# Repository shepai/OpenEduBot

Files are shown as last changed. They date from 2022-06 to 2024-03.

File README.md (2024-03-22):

# OpenEduBot
Python library and robotics building instructions for robotics education within schools. The aim of this project is to provide ease of teaching and programming with MicroPython, and reduce the cost of teaching robotics. Teaching physical robotics is engaging and rewarding. Students gain experience in coding, engineering and electronics, compared to making cheap existing kits that do not combine any of these.

## Robot library
We have written a robotics library that allow connection with each chassis. The library must be placed in the same directory as the code running on the Pico. This can be done using [Thonny IDE](https://thonny.org/)

Once the library is installed on the device.

There are two variants of the library, a circuitPython and a microPython. The circuitPython can work with both the Pico and PiMaker rp2040. The microPython one is designed for the Raspberry Pi Pico. 

## Building a chassis
This Github contains the instructions and demo code for each chassis. Parts lists can be found under each robot, as well as links to places the parts can be purchased. The item names are there, so it is up to you where you purchase thee parts from.

## The different bots
The robots all make use of the Raspberry Pi Pico, which allows programming through Python! Python is a simple language to learn for those starting to learn code.

### WheelBot
Wheelbot uses two DC motors and a ball caster at the front. This robot uses a simple design, but can exhibit some intelligent behaviour. Whether you want to use ultrasound sensors to make robot vacum-cleaner algorithms, or light following bots - your imagination (and the use of wheels) is your limit.

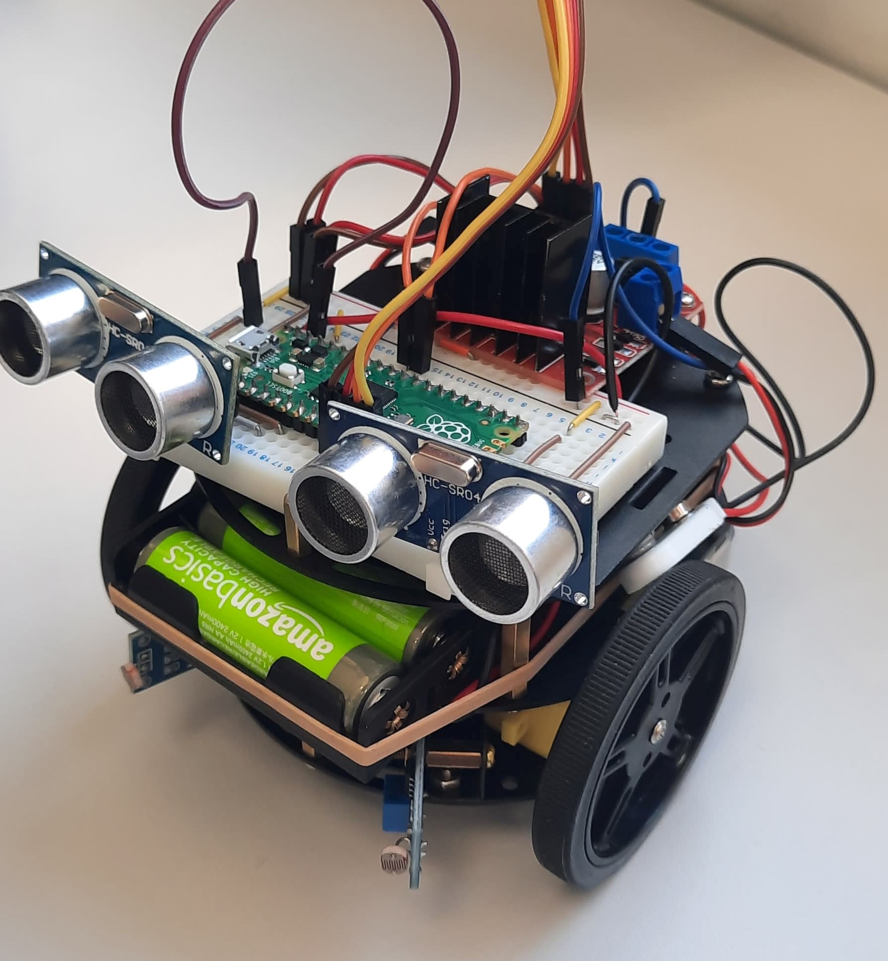
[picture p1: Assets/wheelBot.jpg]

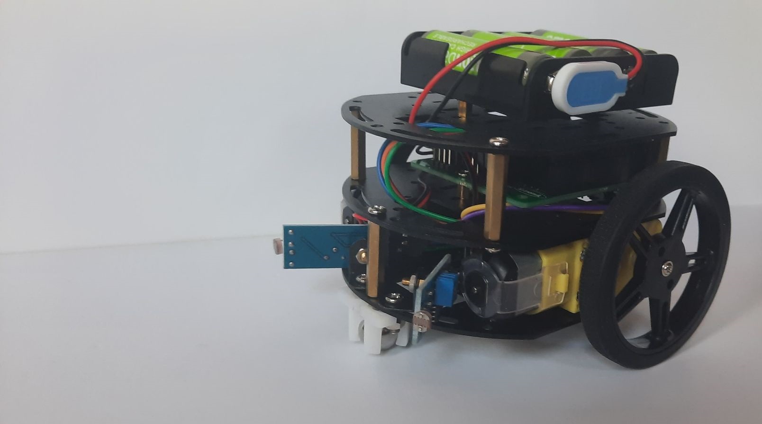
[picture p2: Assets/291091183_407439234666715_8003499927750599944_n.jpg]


## Credits
This project was worked on by University of Sussex students:

Dexter R Shepherd*, https://www.linkedin.com/in/dexter-shepherd-1a4a991b8/

Joshua Kybett, https://www.linkedin.com/in/jkybett/

Eliseo Dalle Crode,https://www.linkedin.com/in/eliseo-dalle-crode-613557104/

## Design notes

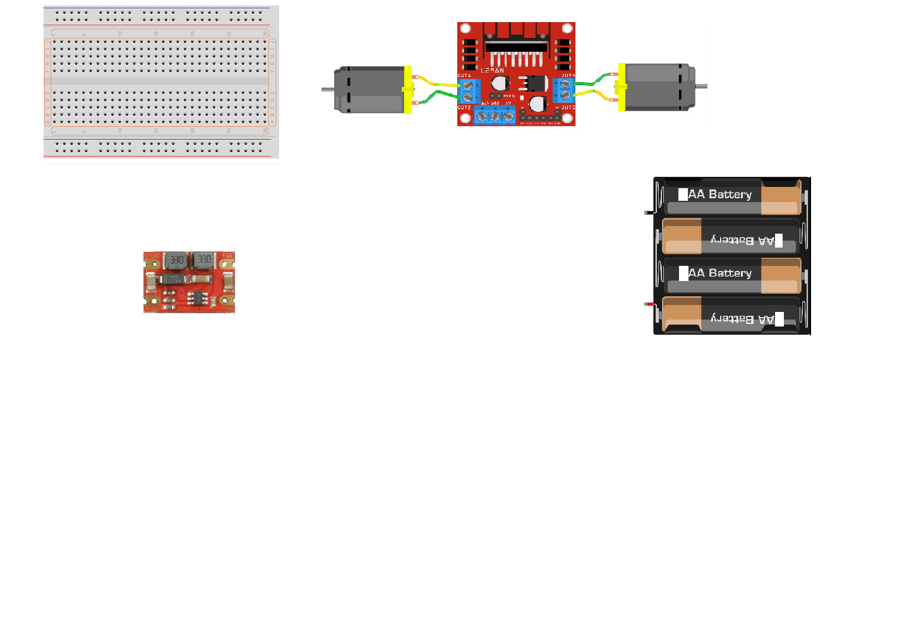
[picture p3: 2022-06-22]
Assets/electronics.png

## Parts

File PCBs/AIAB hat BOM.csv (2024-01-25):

Designator | Footprint | Quantity | Comments | Supplier and ref
HP4067 | SSOP-24_5.3x8.2mm_P0.65mm | 1 | SSOP-24_5.3x8.2mm_P0.65mm
R12,R5,R6,R7 | R_0603_1608Metric | 4 | 1k
APM | PinHeader_1x05_P2.54mm_Vertical | 1 | PinHeader_1x05_P2.54mm_Vertical
C6 | C_0603_1608Metric | 1 | 10uF
D1,D2 | R_LDR_5.1x4.3mm_P3.4mm_Vertical | 2 | R_LDR_5.1x4.3mm_P3.4mm_Vertical
C5 | C_0603_1608Metric | 1 | 4.7uF
Ultra sound,F2,F1 | PinHeader_1x04_P2.54mm_Vertical | 3 | PinHeader_1x04_P2.54mm_Vertical
X1 | MICROSD | 1 | MICROSD
C4 | C_0603_1608Metric | 1 | 220pF
Powerswitch | SW_DIP_SPSTx01_Slide_6.7x4.1mm_W6.73mm_P2.54mm_LowProfile_JPin | 1 | SW_DIP_SPSTx01_Slide_6.7x4.1mm_W6.73mm_P2.54mm_LowProfile_JPin
M12,M11,Power | TerminalBlock_Altech_AK300-2_P5.00mm | 3 | TerminalBlock_Altech_AK300-2_P5.00mm
I2C,POWER2,AP | PinHeader_1x02_P2.54mm_Vertical | 3 | PinHeader_1x02_P2.54mm_Vertical
C4M | 0805-NO | 1 | 10uF
PI | RPi_Pico_SMD_TH | 1 | RPi_Pico_SMD_TH
MDrive | DIP-16_W10.16mm | 1 | DIP-16_W10.16mm
R2,R1,R3,R4 | R_0603_1608Metric | 4 | 4.7k
R8 | R0805 | 1 | 1K
VR | SOT-223-3_TabPin2 | 1 | SOT-223-3_TabPin2
C7,C2,C1,C3 | C_0603_1608Metric | 4 | 0.1uF
R11,R10 | RESPACK_4X0603 | 2 | 10K
C2B | E3,5-8 | 1
U1 | TSSOP28 | 1 | PCA9685
IC1 | SO16 | 1 | 4050D
D3 | LED_0603_1608Metric | 1 | LED_Small_Filled
U2 | SOT-23-5 | 1 | AP2112K-3.3
U4 | InvenSense_QFN-24_4x4mm_P0.5mm | 1 | MPU-6050
ACT0 | CHIP-LED0805 | 1 | RED
JP2 | 3X04 | 1
R9 | RESPACK_4X0603 | 1 | 220

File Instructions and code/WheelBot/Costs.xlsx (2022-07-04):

 |  |  |  | No. of robots
 |  |  |  | 1
One robot
Part | Quantity | Price | Subtotal | Link |  |  |  |  |  | Key
Chassis | 1 | 23.7 | 23.7 | https://thepihut.com/products/adafruit-mini-3-layer-round-robot-chassis-kit-2wd-with-dc-motors |  |  |  |  |  | PiHut
Robotics HAT | 1 | 13.75 | 13.75 | https://uk.rs-online.com/web/p/raspberry-pi-hats-add-ons/2247771 |  |  |  |  |  | RS
Battery holder | 1 | 0.808 | 0.808 |  |  |  |  |  |  | Amazon
Batteries | 4 | 0.608 | 2.432 |  |  |  |  |  |  | Farnell
Screwdriver set | 1 | 0.8106666667 | 0.8106666667
Pico | 1 | 3.276 | 3.276
USB cable | 1 |  | 0
Battey wire | 1 | 0.317 | 0.317 |  |  |  | Overall total | Tax estimate | Total estimate
Sensors | 4 | 0.5592 | 2.2368 |  |  |  | £1700.30 | £340.06 | £2040.36
Bracket | 4 | 0.0932 | 0.3728
Jumper wires | 12 | 0.03745 | 0.4494
M3 screws | 12 | 0.21 | 2.52
GPIO pins | 40 | 0.003596 | 0.14384
Standoffs | 6 | 0.176 | 1.056
Total | 89 | £44.35 | £51.87
Mass parts | Price | Per unit | Pack No. | Min Quantity | Subtotal | Link
480 Picos | 1572.48 | 3.276 | 480 | 1 | 1572.48 | https://uk.rs-online.com/web/p/raspberry-pi/2122161
Jumper wire pack | 7.49 | 0.03745 | 200 | 1 | 7.49 | https://www.amazon.co.uk/AZDelivery-Jumper-Arduino-Raspberry-Breadboard/dp/B07KFMSW7H
Battery wire 100 | 31.7 | 0.317 | 100 | 1 | 31.7 | https://uk.rs-online.com/web/p/battery-contacts/0489021A
Brackets | 5.592 | 0.0932 | 60 | 1 | 5.592 | https://www.amazon.co.uk/gp/product/B07RBJN9YF/ref=ppx_yo_dt_b_search_asin_title?ie=UTF8&psc=1
Battery pack (25) | 20.2 | 0.808 | 25 | 1 | 20.2 | https://uk.farnell.com/multicomp-pro/mp000316/battery-holder-aa-snap-on/dp/3126550
GPIO pins | 7.192 | 0.003596 | 2000 | 1 | 7.192 | https://www.amazon.co.uk/Pack-Single-2-54-Header-Connector/dp/B06XR8CV8P
MH sensor 10 | 5.592 | 0.5592 | 10 | 1 | 5.592 | https://www.amazon.co.uk/DollaTek-Digital-Intensity-Resistor-Photoresistor/dp/B07DJ4CMF7
GPIO pins bent | 8.4 | 0.84 | 10 | 1 | 8.4 | https://uk.farnell.com/samtec/tsm-106-01-l-sv/header-2-54mm-smt-1x6way/dp/1885916?mckv=_dc|pcrid|565467377247|plid||kword||match||slid||product|1885916|pgrid|125527087130|ptaid|pla-1641699961606|&CMP=KNC-GUK-GEN-SHOPPING-SMART-AUTOMATION-MEDIUMROAS-Test860&gross_price=true
M3 screws | 3.42 | 0.21 | 100 | 1 | 3.42 | https://uk.rs-online.com/web/p/self-tapping-screws/4831202
Screwdriver set | 2.432 | 0.8106666667 | 3 | 1 | 2.432 | https://www.amazon.co.uk/Screwdriver-Electrical-Precision-Non-Slip-Professional/dp/B07R6SVFSV
Batteries | 7.296 | 0.608 | 12 | 1 | 7.296 | https://www.amazon.co.uk/AmazonBasics-Pre-Charged-Rechargeable-Batteries-Packaging-Black/dp/B007B9NXAC
Standoffs bag 100 | 20.98 | 0.176 | 100 | 1 | 20.98 | https://uk.rs-online.com/web/p/standoffs/2808878
Total | £1692.77 | £7.74 |  |  | £1692.77

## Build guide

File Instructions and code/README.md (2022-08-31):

# Introduction

There are different chassis that the library currently supports. Of course, you can build and make your own, but these are the chassis we have built support for.

For both the wheelbot_2 chassis variants, the Raspberry Pi Pico Robotics board has support for both circuitpython and micropython. [The uf2 file is available here for Pi Pico circuitPython](https://raw.githubusercontent.com/shepai/OpenEduBot/main/Assets/adafruit-circuitpython-cytron_maker_pi_rp2040-en_GB-7.3.2.uf2).

## MicroPython
MicroPython is the default on the Raspberry Pi Pico. The Raspberry Pi Pico can be converted to use CircuitPython, and vice versa. Our library supports both the PiMaker board and the pico on the CircuitPython variant.

### [WheelBot for motor driver](https://github.com/shepai/OpenEduBot/tree/main/Instructions%20and%20code/WheelBot_old)
Wheelbot is a robot that uses... wheels and a ball caster. It is  great for line following, obstacle avoiding, and light following tasks. This small cheap chassis can allow cheap robotics teaching in schools. This makes use of motor drivers and breadboards, allowing you to build your own circuits. This robot is better for teaching electronic tasks, and good for audience who require longer.



### [WheelBot](https://github.com/shepai/OpenEduBot/tree/main/Instructions%20and%20code/WheelBot)
Wheelbot is an updated version of the older wheelbot that uses motor drivers, to use a better, more compact circuit. This robot can also be cheaper than the older wheelbot. This method requires little circuit building compared to wheelbot, making it quicker to build and deploy for any audience.



There is also a slick variant of the chassis that you can build on two layers. This is our newer design which is more compact and easier to construct.

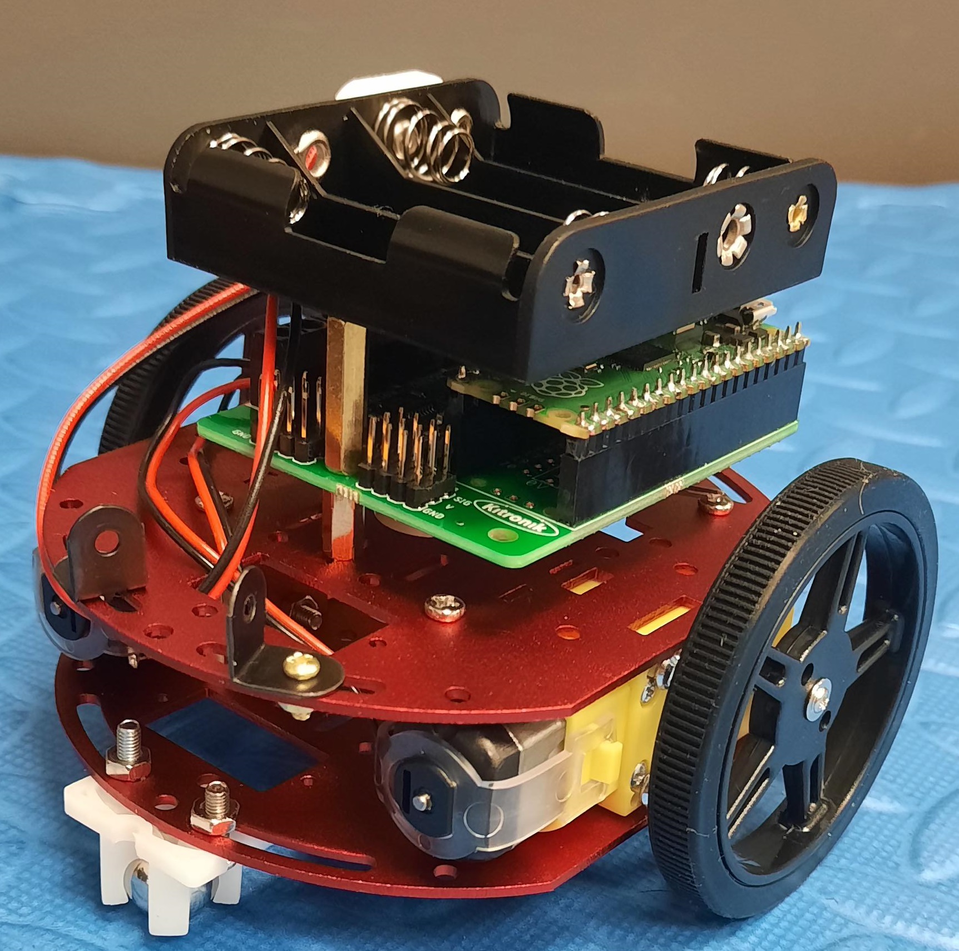
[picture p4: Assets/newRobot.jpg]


We recommend purchasing assorted spacers/standoffs of 2.5mm for mounting electronics. Depending on your circuit layout and what you include, having a larger number of spaces gives you more options.

### [ServoBot](https://github.com/shepai/OpenEduBot/tree/main/Instructions%20and%20code/ServoBot)
Servo bot is in development, and will allow you to control two wheels via continuous rotation servos. Continuous rotation servos typically have a threshold screw joint, if you find that your motors are rotating when you have not made them it is likely you will need to turn the threshold till they stop moving. Be aware that the equilibrium can only be set when the motors have been issued a stop command and are still rotating.

## CircuitPython

CircuitPython is an alternative to MicroPython that some devices use. Using EduBot_CP.py you can have access to CircuitPython variants of the chassis. These will have separate instructions.

### [WheelBot](https://github.com/shepai/OpenEduBot/tree/main/Instructions%20and%20code/CircuitPython%20WheelBot)
This is a CircuitPython variant for the wheelbot. This has a braitenberg example for light following behaviours.
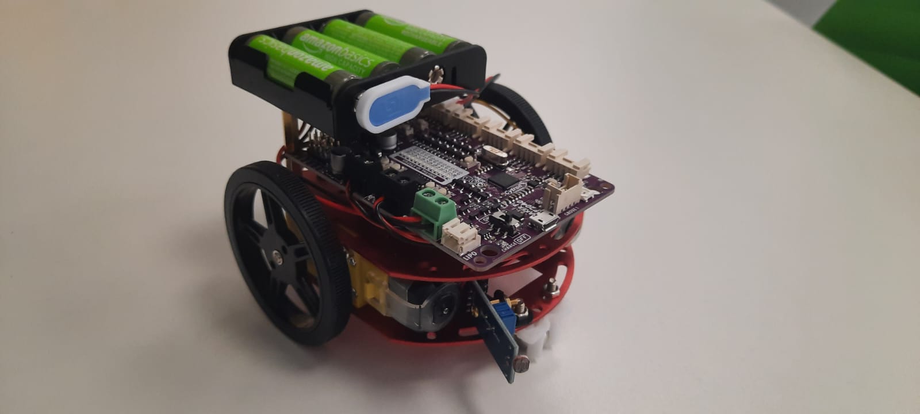
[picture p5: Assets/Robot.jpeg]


This is called in within the same way as the wheelbot_2, and you can also use this same tutorial on the micropython Pico variant. Make sure you install the uf2 file onto the Pico so that it is ready for circuitPython. The only difference is you will need to tell the object what the board type is:

```
from EduBot_CP import wheelBot_2

bot = wheelBot_2(board_type="pico")
```

## Controlling sensors
The different example codes come with their own sensor control. This section explains how you can use different sensors an interface with them.

### Photoresistor light sensors
The Photoresistor light sensor typically has 3 or 4 pins. The 3 pin variant is designed for digital reading. This will mean that the light detects on or off based on the light level crossing a threshold. The light threshold activation can be determined by rotating the screw in the blue box. With the 4 pin variant you have the choice between digital and analogue. Analogue is better at reading the intensity of light on a scale. This is ideal for light following robots.

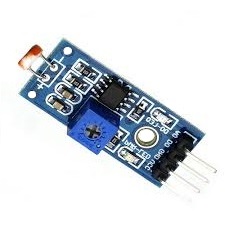
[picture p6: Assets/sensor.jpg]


Within MicroPython we can call pins in using the machine library. We can then set a pin number using one of the GP#. Here we have pin 27 set to digital read and pin 26 set to analogue.

```
from machine import Pin,ADC

digital_pin=Pin(27,Pin.IN)
analog_pin=ADC(26)

print(digital_pin.value())
print(analog_pin.read_u16())
```

The above code will execute and print a digital reading of 1 or 0, depending on whether the sensor threshold is met. It will then output an analogue reading from the sensor connected to 26. This can be a very large and noisy value. You may want to see what the maximum and minimum values it can reach and divide down to a percentage scale of what it was. This is especially good when you are controlling motor speeds based off of light intensity.

Within CircuitPython the digital and analogue pins are separate libraries. We also must import board in order to get easy access to each pin. The following codes both use the same pins as the micropython code above.

```
import board
from analogio import AnalogIn

s1 = AnalogIn(board.GP26)

def get_voltage(pin):
    return (pin.value * 3.3)

print(get_intensity(s1))
```

For digital reading we use the digital library.

```
import board
from digitalio import DigitalInOut, Direction, Pull

s2 = DigitalInOut(board.GP27)
s2.direction = Direction.INPUT

print(s2.value)

```

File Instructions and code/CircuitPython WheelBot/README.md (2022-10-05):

# WheelBot CircuitPython
The WheelBot2 chassis can be implemented using a number of different dc motor controlled chassis. The one we have used was purchased from the [Pi Hut](https://thepihut.com/products/adafruit-mini-3-layer-round-robot-chassis-kit-2wd-with-dc-motors). For electronics it required the following items:
- [PiMaker](https://thepihut.com/products/maker-pi-rp2040)
- One 4xAA battery holder
- Ultrasound range finders (optional)
- IR light sensors (optional)
- Light sensitivity sensors (optional)
- AA batteries 4



You can also use the Raspberry Pi Pico with CircuiPython by flashing it with the correct [uf2 file](https://circuitpython.org/downloads). This means the library supports different boards and different motor controllers. This uses the PiMaker, or can use a Pico with the Kitroniks robotics board or Kitroniks motor driver. Selecting between either of them can be done in the library [(See documentation)](https://github.com/shepai/OpenEduBot/tree/main/Library)
## Building the chassis
Firstly you will need to get the following parts. These parts can be found in the excel spreadsheet "costs.xlsx". It approximately costs £50 a robot. The more you build, the cheaper they become.

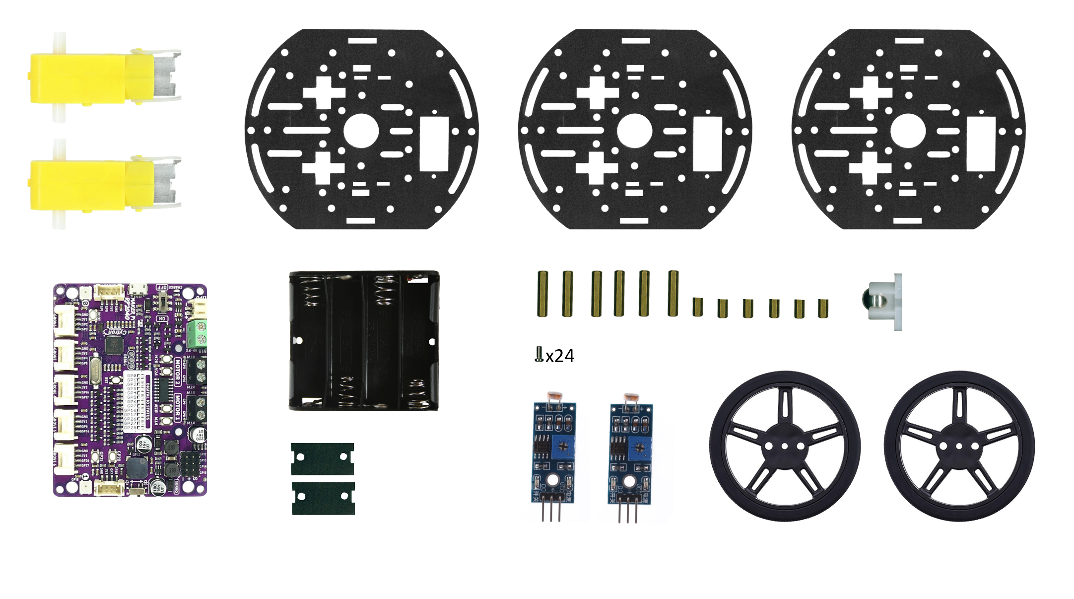
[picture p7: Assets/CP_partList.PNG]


### Wiring

The wiring of the motors and battery needs to be in motors 3 and 4 for the library to be compatible. You may want to strip the ends of the wires off on the motors if it cannot be directly screwed into the robotics board.
The sensor inputs can be changed to any analogue pin, if you wish to add more then they can be used.

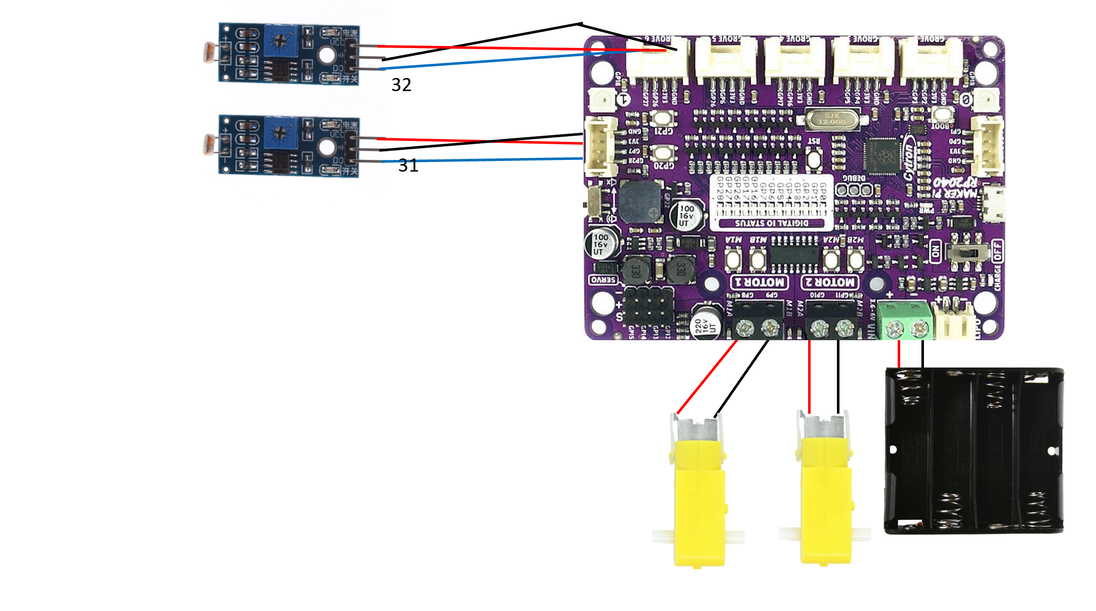
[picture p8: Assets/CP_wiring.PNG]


### Step 1
Mount both of the motors on the chassis, using the side plates within the two rectangular slots on the chassis will keep the motors in place. This is the point that you can mount your chosen sensors for the lower level. If you are working with light sensors, this level is ideal.

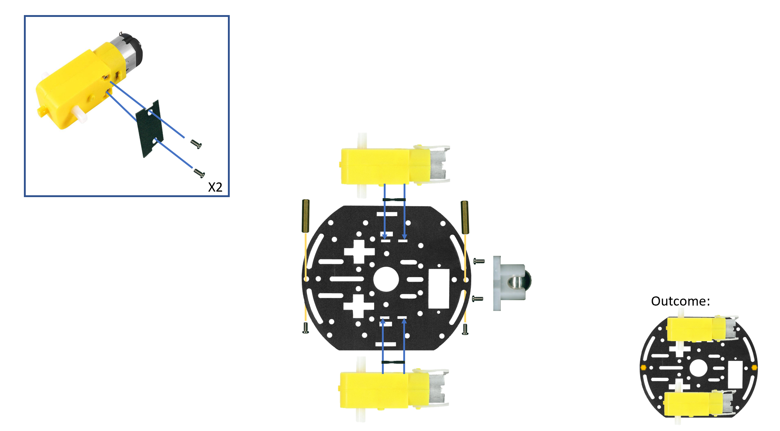
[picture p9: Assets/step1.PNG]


### Step 2
Mount the main controller, make sure you have soldered some L-shaped pins underneath the Robotics board if you wish to use GPIO pins to interface with sensors. If you are using more HATs than just the robotics board, you may want to consider using Step 3 as your second layer.
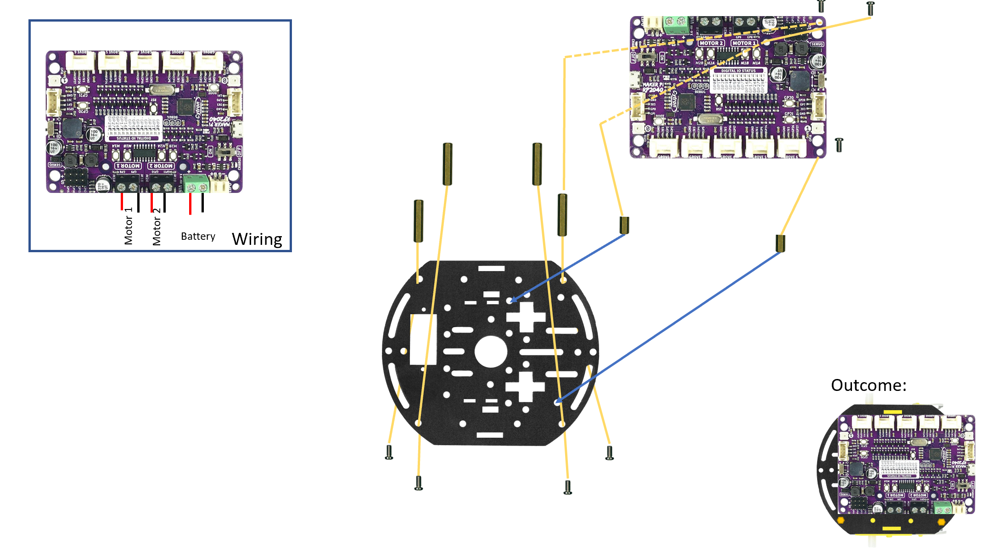
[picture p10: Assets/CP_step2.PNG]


### Step 3
It is ideal to have the batteries on the top, so they can be easily changed without having to unscrew the chassis.
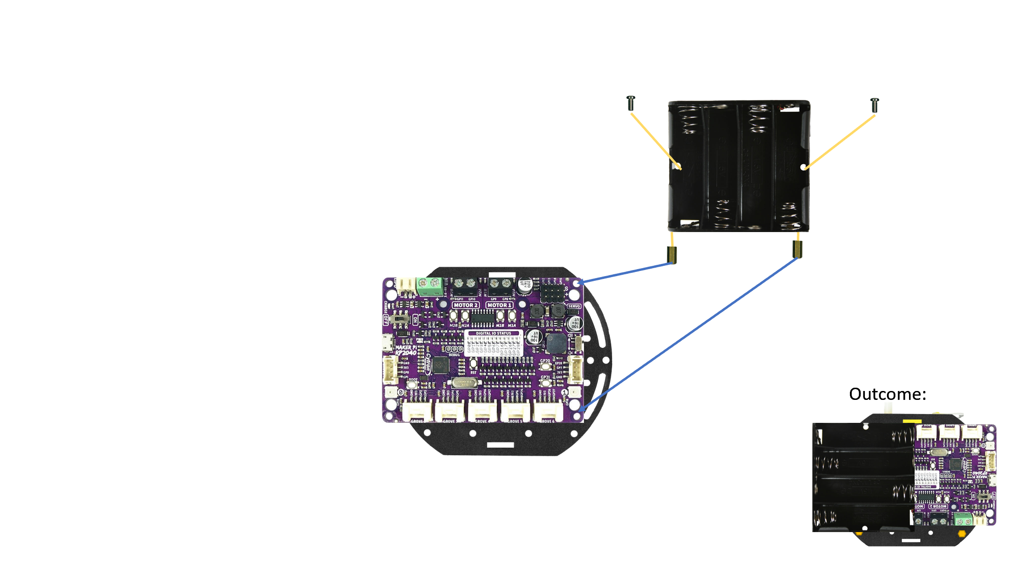
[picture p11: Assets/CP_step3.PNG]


## Programming

The physical robot makes use of sensors and two motors. We can attach a USB to it and upload the code.

## Using a different IDE
Using a specific IDEs can be simpler for using MicroPython. [Thonny IDE](https://thonny.org/) is a simple IDE for uploading programs to the Raspberry Pi Pico. Once you have set up the IDE we can start [programming the board](https://projects.raspberrypi.org/en/projects/getting-started-with-the-pico).

### Step 1
Download the robot control library from [Github](https://raw.githubusercontent.com/shepai/OpenEduBot/main/Library/EduBot_CP.py) and have handy in a folder.

### Step 2
You will need to connect the robot to your device via USB. Make sure you have Thonny IDE up. In the bottom right corner you should be able to select the interpreter for the IDE. We want Generic CircuitPython.

## Troubleshooting
There are some problems that you may come into contact with, especially if this is your first time to electronics. We have tried to list as many here as we can. If your problem is not listed, please see [issues](https://github.com/shepai/OpenEduBot/issues) and if there still isn't an answer feel free to raise one yourself!

### The board wont connect to USB
Firstly, make sure your USB device works for data transmission. Check your wiring and make sure there is no short circuiting. If this is all fine, consider having the battery switched on while you make contact with the board. We suspect there is an issue with the current being supplied to the device and it not being seen by the PC.

### The sensors aren't working
Check your wiring, also make sure the sensors are not touching the motor pins or conducting where they should not.

### The motors are turning the wrong way
There are two ways to solve this, hardware or software. Firstly make sure that the motors are wired the same. Red Black Red Black should be the pattern going in to the device. Within the examples, you can change the motors to be of speed *-1 to reverse the motors.

```
bot.motor1_move(max(r1,20) *-1) #remove *-1 for alternate direction
bot.motor2_move(max(r2,20))
```

### The motors are not turning at allow
Make sure the motors are both the sockets. The board should be on and your code running. Solder over the outside of the motor wire tips if you can, this prevents short circuiting.

### The light detecting robot is moving away from Light
This is likely because your sensors are the wrong way round. Try changing the pins physically or switching the pins in the code.

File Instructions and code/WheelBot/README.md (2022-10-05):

# WheelBot
The WheelBot chassis can be implemented using a number of different dc motor controlled chassis. The one we have used was purchased from the [Pi Hut](https://thepihut.com/products/adafruit-mini-3-layer-round-robot-chassis-kit-2wd-with-dc-motors). For electronics it required the following items:
- Raspberry Pi Pico
- [Robotics Hat](https://thepihut.com/products/robotics-board-for-raspberry-pi-pico)
- One 4xAA battery holder
- Ultrasound range finders (optional)
- IR light sensors (optional)
- Light sensitivity sensors (optional)
- AA batteries 4

You should be able to build a working one of these for approx £30-£50 each depending on bulk buy and how much you are willing to solder. This robot is very similar to the WheelBot robot, but with one key difference - which is the robotic hat. This hat is more expensive than using a motor driver but much more compact for the chassis. Additionally, it has an inbuilt voltage regulator so both the Pico and hat can be powered from one battery holder.

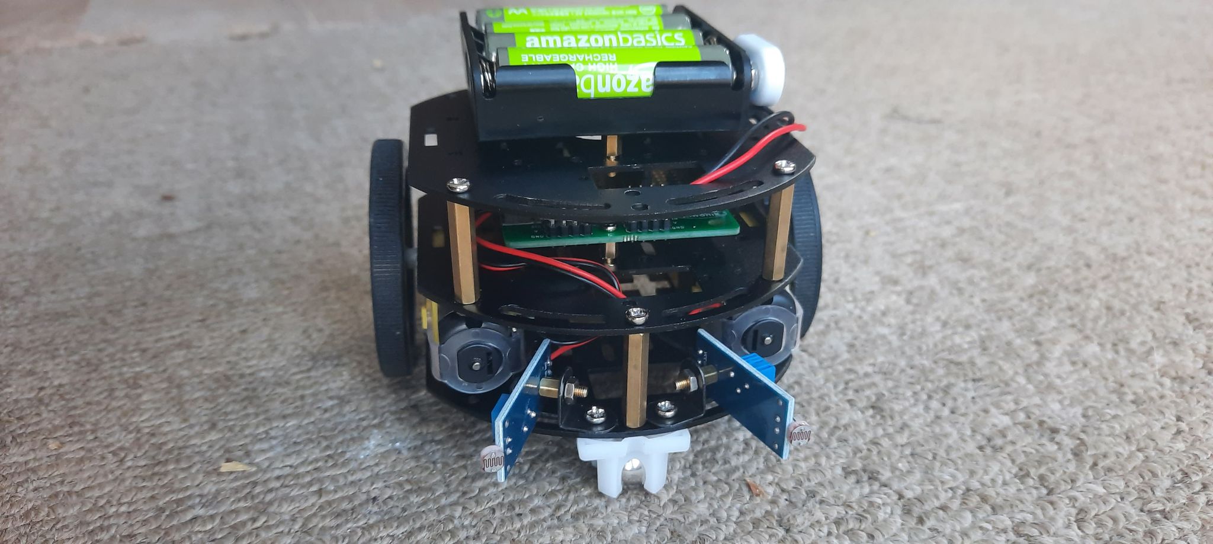
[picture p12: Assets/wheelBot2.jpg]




This page has instructions to build the first chassis, but the second chassis can be built in a similar way. The motor and ball assembly remains the same.

The Pico can be flashed with circuitPython should you need access to libraries such as [ulab](https://docs.circuitpython.org/en/latest/shared-bindings/ulab/index.html) (cp variant of numpy)

The robot can use the Kitroniks motor driver and the Kitroniks robotics board. Selecting between either of them can be done in the library [(See documentation)](https://github.com/shepai/OpenEduBot/tree/main/Library)

## Building the chassis
Firstly you will need to get the following parts. These parts can be found in the excel spreadsheet "costs.xlsx". It approximately costs £50 a robot. The more you build, the cheaper they become.

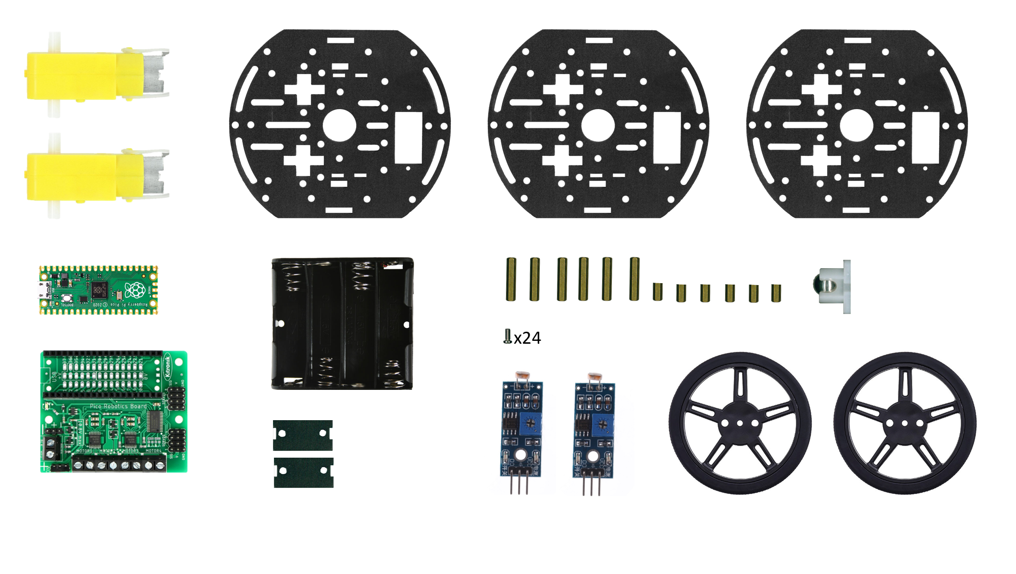
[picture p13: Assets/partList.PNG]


### Wiring

The wiring of the motors and battery needs to be in motors 3 and 4 for the library to be compatible. You may want to strip the ends of the wires off on the motors if it cannot be directly screwed into the robotics board.
The sensor inputs can be changed to any analogue pin, if you wish to add more then they can be used.

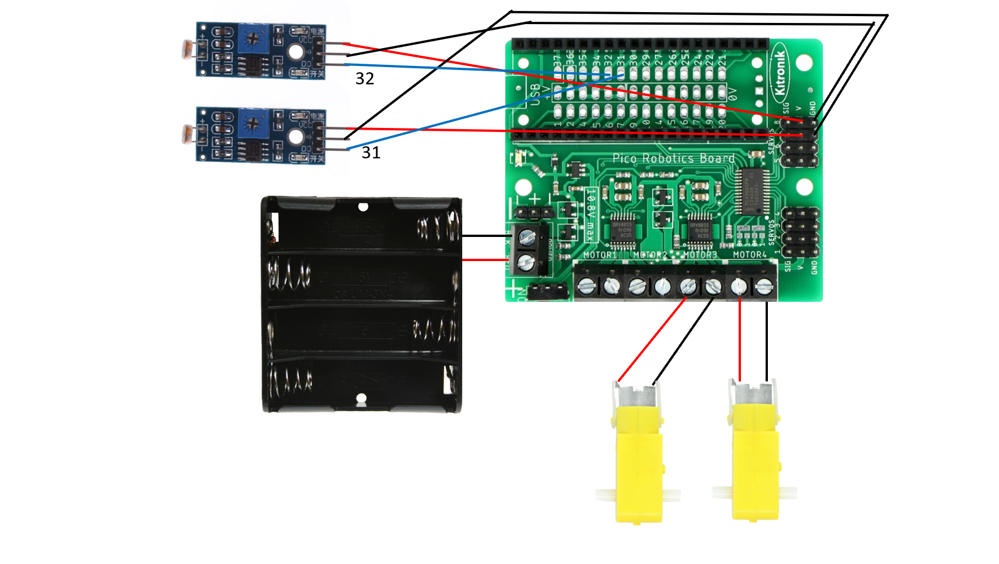
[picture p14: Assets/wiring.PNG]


### Step 1
Mount both of the motors on the chassis, using the side plates within the two rectangular slots on the chassis will keep the motors in place. This is the point that you can mount your chosen sensors for the lower level. If you are working with light sensors, this level is ideal.



#### Step 1.1 - Roller ball wheel
Mount the roller ball wheel inserting the screws from the bottom. If using sensors, mount the L-shaped bracket along with the roller ball wheel.

#### Step 1.2 - Light Sensors
Mount the light sensors to the L-brackets using a small standoff to offset the sensors.

#### Step 1.3 - 2nd Layer standoffs
Attach 4 long standoffs in the corners of the 2nd layer, along with 2 small standoffs to mount the main controller board.

### Step 2
Mount the main controller, make sure you have soldered some L-shaped pins underneath the Robotics board if you wish to use GPIO pins to interface with sensors. If you are using more HATs than just the robotics board, you may want to consider using Step 3 as your second layer.
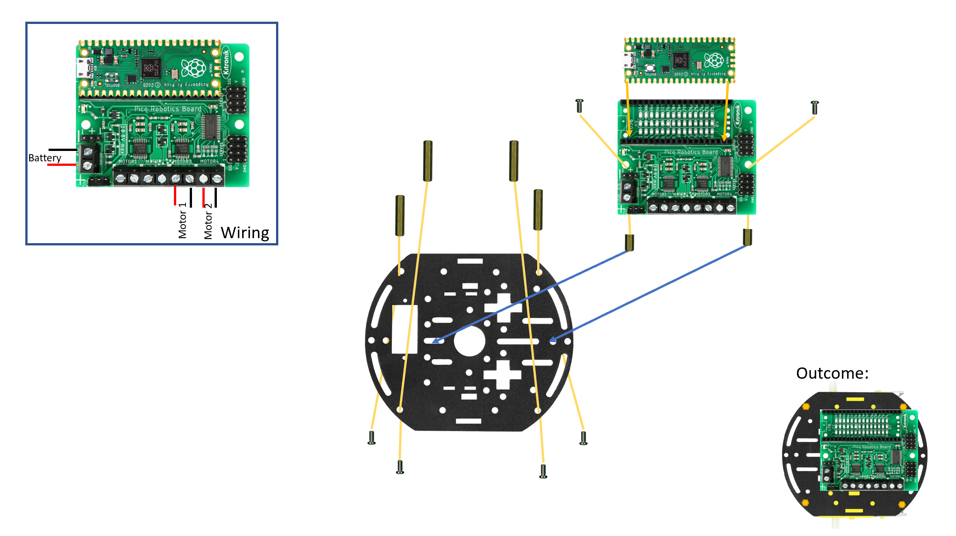
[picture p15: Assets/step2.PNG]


### Step 3
It is ideal to have the batteries on the top, so they can be easily changed without having to unscrew the chassis.
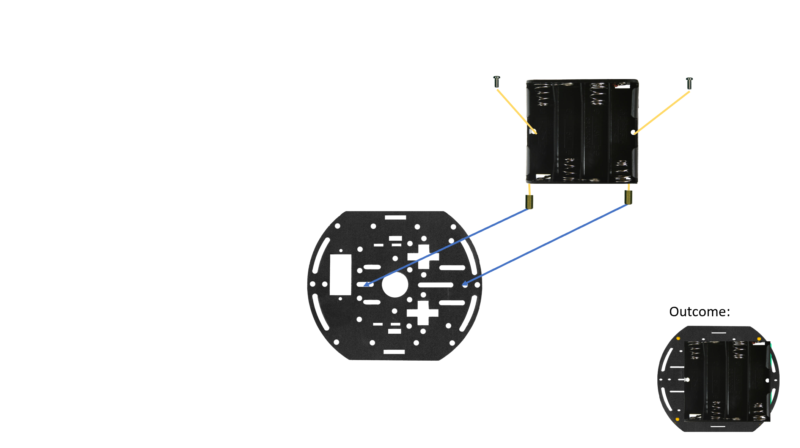
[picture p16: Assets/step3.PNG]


#### Step 3.1 Wiring
Wire the motors into the motor controller connections on the main controller. Left/Right motor connections are interchangable in the software so do not worry about mixing them.

#### Step 3.2 Battery Wiring
Attach the battery connector into the Power BLK+RED connections on the main controller.

#### Step 3.3 Sensor Wiring
If using sensors, wire them up to the servos pins on the main controller, a single wire from the sensors should be connected to the L-shaped GPUIO pins that were soldered on the underside for the controller.

### Step 4 - 3rd Layer
Mount the battery holder using a 2 double ended threaded pieces and 4 screws. Then mount the 3rd layer to the 4, 2nd layer standoffs. Then attach the battery connector to the holder.

## Programming

The physical robot makes use of sensors and two motors. We can attach a USB to it and upload the code.

## Using a different IDE
Using a specific IDEs can be simpler for using MicroPython. [Thonny IDE](https://thonny.org/) is a simple IDE for uploading programs to the Raspberry Pi Pico. Once you have set up the IDE we can start [programming the board](https://projects.raspberrypi.org/en/projects/getting-started-with-the-pico).

### Step 1
Download the robot control library from [Github](https://raw.githubusercontent.com/shepai/OpenEduBot/main/Library/EduBot.py) and have handy in a folder.

### Step 2
You will need to connect the robot to your device via USB. Make sure you have Thonny IDE up. In the bottom right corner you should be able to select the interpreter for the IDE. We want Raspberry Pi Pico MicroPython.



The software will ask you to install firmware for the Pico. Install it.



The shell should then show it is connected to the Pico. Try entering the following in the shell:

```
print("Hello, world!")
```

This code is compiling on the Pico board. Any code they you write and run will now be uploading to the device.

### Step 3
Open the downloaded EduBot.py in the Thonny IDE, and then go to File>Save As and a prompt will come up asking whether to install on the device or computer. Resave the file on the device with the same name. We do this so we can control the chassis hardware.

Pre-written examples can be found:
- Example.py

The EduBot.py found in [library](https://github.com/shepai/OpenEduBot/Library) must be uploaded in the same directory as your main code on the Raspberry Pi Pico.

We have used the [Thonny IDE](https://thonny.org/). Once downloaded this software allows you to connect to the Raspberry Pi Pico. Simply go to the bottom right corner of the window, and select an interpreter. We are using the Raspberry Pi Pico. Raspberry Pi have a [tutorial](https://projects.raspberrypi.org/en/projects/getting-started-with-the-pico) on getting set up with the Pico.

Once all connected you can load one of our examples in and click run. The robot will run this code while the USB is attached. To make it mobile, save the example as main.py on the Pico device, and it will run on boot.

## Troubleshooting
There are some problems that you may come into contact with, especially if this is your first time to electronics. We have tried to list as many here as we can. If your problem is not listed, please see [issues](https://github.com/shepai/OpenEduBot/issues) and if there still isn't an answer feel free to raise one yourself!

### The board wont connect to USB
Firstly, make sure your USB device works for data transmission. Check your wiring and make sure there is no short circuiting. If this is all fine, consider having the battery switched on while you make contact with the board. We suspect there is an issue with the current being supplied to the device and it not being seen by the PC.

### The sensors aren't working
Check your wiring, also make sure the sensors are not touching the motor pins or conducting where they should not.

### The motors are turning the wrong way
There are two ways to solve this, hardware or software. Firstly make sure that the motors are wired the same. Red Black Red Black should be the pattern going in to the device. Within the examples, you can change the motors to be from "f" to "r" or vice versa.

### The motors are not turning at allow
Make sure the motors are both in the motor 2 and motor 4 sockets. The board should be on and your code running. Solder over the outside of the motor wire tips if you can, this prevents short circuiting.

### The light detecting robot is moving away from Light
This is likely because your sensors are the wrong way round. Try changing the pins physically or switching the pins in the code.

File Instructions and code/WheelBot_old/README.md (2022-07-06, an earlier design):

# WheelBot
The WheelBot chassis can be implemented using a number of different dc motor controlled chassis. The one we have used was purchased from the [Pi Hut](https://thepihut.com/products/adafruit-mini-3-layer-round-robot-chassis-kit-2wd-with-dc-motors). For electronics it required the following items:
- Raspberry Pi Pico
- Motor driver (L298N)
- A selection of jumper wires
- One 4xAA battery holder
- One 3xAA battery holder or some form of [voltage regulator](https://thepihut.com/products/dc-dc-automatic-step-up-down-power-module-2-5-15v-to-3-3v-600ma)
- Ultrasound range finders (optional)
- IR light sensors (optional)
- Light sensitivity sensors (optional)
- AA batteries (between 4-6 depending on your battery option)

You should be able to build a working one of these for approx £30-£50 each depending on bulk buy and how much you are willing to solder.  



## Building the chassis

### battery options
There are two battery options that you can take to powering your robot. The Pico uses 3.3v whereas the motor driver requires a minimum of 5V. Using 4AA batteries we can produce over 5V and make the motors operate well. However, we cannot power the Pico directly from that as we risk damaging it. The simple solution is to run two separate battery packs, one with three AAs and one with four. As long as the ground is concocted this will function.

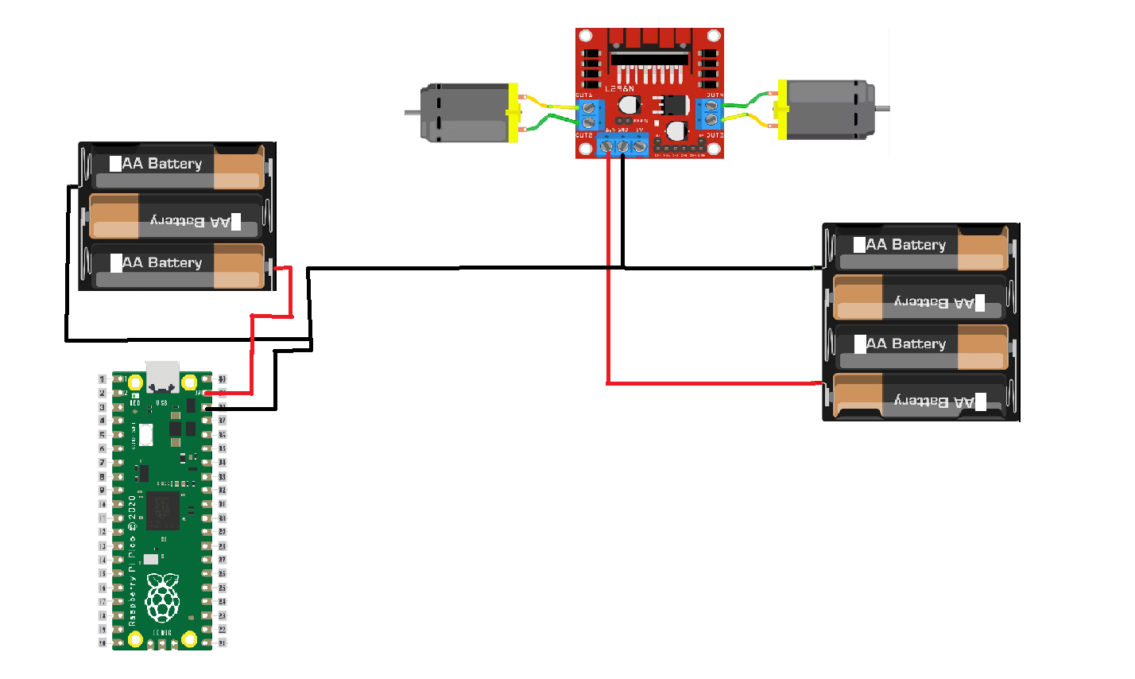
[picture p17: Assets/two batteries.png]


The second option is more eloquent and less "clunky" which makes use of a voltage regulator. This steps down the voltage to a suable 3.3V for the Pico, and runs everything off of the same battery. We should always show caution using the same battery with robotics as motors can have a high current draw, causing the main controller to shut down/ reboot.

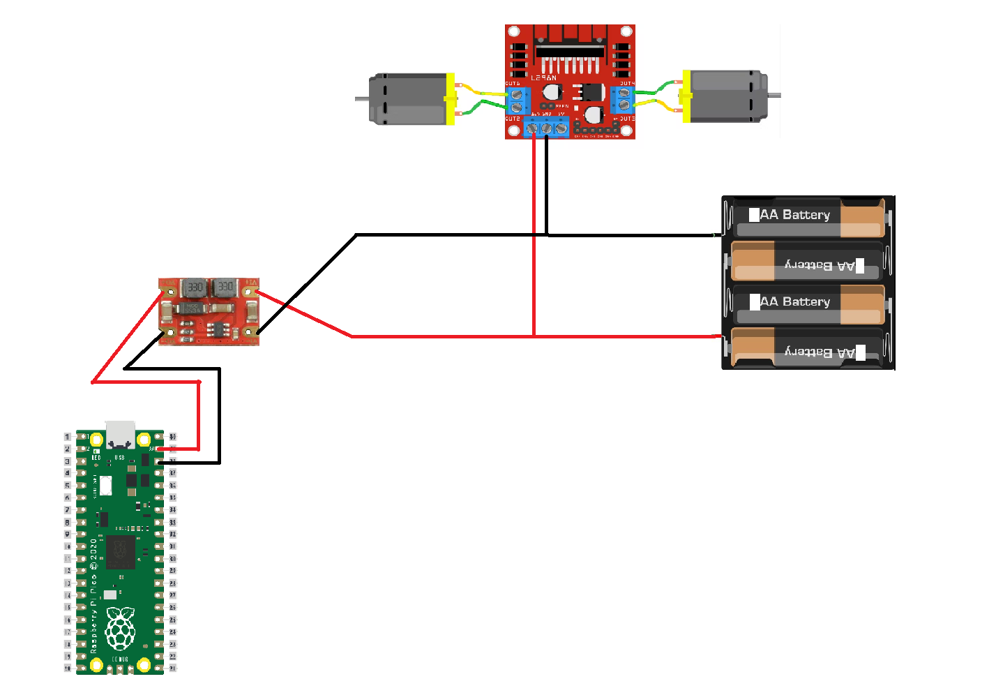
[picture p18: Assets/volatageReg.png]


## Programming

The physical robot makes use of sensors and two motors. We can attach a USB to it and upload the code.

## Using a different IDE
Using a specific IDEs can be simpler for using MicroPython. [Thonny IDE](https://thonny.org/) is a simple IDE for uploading programs to the Raspberry Pi Pico. Once you have set up the IDE we can start [programming the board](https://projects.raspberrypi.org/en/projects/getting-started-with-the-pico).

### Step 1
Download the robot control library from [Github](https://raw.githubusercontent.com/shepai/OpenEduBot/main/Library/EduBot.py) and have handy in a folder.

### Step 2
You will need to connect the robot to your device via USB. Make sure you have Thonny IDE up. In the bottom right corner you should be able to select the interpreter for the IDE. We want Raspberry Pi Pico MicroPython.



The software will ask you to install firmware for the Pico. Install it.



The shell should then show it is connected to the Pico. Try entering the following in the shell:

```
print("Hello, world!")
```

This code is compiling on the Pico board. Any code they you write and run will now be uploading to the device.

### Step 3
Open the downloaded EduBot.py in the Thonny IDE, and then go to File>Save As and a prompt will come up asking whether to install on the device or computer. Resave the file on the device with the same name. We do this so we can control the chassis hardware.

Pre-written examples can be found:
- Example.py
- obstacle avoid.py
- All the files within the folder Braitenberg

These files use different sensors, so make sure you have purchased the correct sensors and wired them to the specified pins for each. This is explained in the comments of each python file.

The EduBot.py found in [library](https://github.com/shepai/OpenEduBot/Library) must be uploaded in the same directory as your main code on the Raspberry Pi Pico.

We have used the [Thonny IDE](https://thonny.org/). Once downloaded this software allows you to connect to the Raspberry Pi Pico. Simply go to the bottom right corner of the window, and select an interpreter. We are using the Raspberry Pi Pico. Raspberry Pi have a [tutorial](https://projects.raspberrypi.org/en/projects/getting-started-with-the-pico) on getting set up with the Pico.

Once all connected you can load one of our examples in and click run. The robot will run this code while the USB is attached. To make it mobile, save the example as main.py on the Pico device, and it will run on boot.

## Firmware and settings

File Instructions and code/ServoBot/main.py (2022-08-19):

"""
Servo robot using continuous rotation motors

Code by Dexter R Shepherd

"""

from EduBot import servoBot
import utime


a=servoBot(1,2)

#go forward
a.servoWrite(1,40)
a.servoWrite(2,140)

utime.sleep(1)

a.servoWrite(1,0)
a.servoWrite(2,0)

"""
for i in range(10):
    a.servoWrite(1,0)
    a.servoWrite(2,0)
    utime.sleep(1)
    a.servoWrite(1,180)
    a.servoWrite(2,180)
    utime.sleep(1)
    """

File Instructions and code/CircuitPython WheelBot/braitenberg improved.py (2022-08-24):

"""
Light braightenberg robot

The sensor pins are read at 26 and 27, if the robot is not turning away from the collision,
consider switching the pins around (26 & 27).

Code by Dexter R Shepherd

 
DEBUGGIN TIPS:

If your robot is running away from light, then you should switch the sensor cables around (or switch the pins in the code)

"""
from EduBot_CP import wheelBot
import time
import board
from analogio import AnalogIn

s2 = AnalogIn(board.GP26)
s1 = AnalogIn(board.GP27)

bot=wheelBot()

#get background noise
ST1=s1.value * 3.3
ST2=s2.value * 3.3


def get_intensity(pin,M=65536):
    return max(min(1-((pin.value * 3.3) / M),1),0)

while True:
    r1,r2=(int(get_intensity(s1,M=ST1)*100),int(get_intensity(s2,M=ST2)*100))

    print(r1,r2)
    
    #move at full speed
    bot.motor1_move(max(r1,20) *-1) #remove *-1 for alternate direction
    bot.motor2_move(max(r2,20))

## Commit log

2022-05-19 wheelbot example code
2022-06-22 Pico connect
2022-06-22 battery options
2022-07-07 wiring photo
2022-08-08 circuit python variant
2022-08-14 led display
2022-08-15 sensor example
2022-08-15 corrected sensor
2022-08-16 cp wheelbot
2022-08-19 sensor docs
2022-08-19 genotype bot read from new sensor
2022-08-19 servo bot updates
2022-08-22 individual motor control
2022-08-22 name change
    [Costs.xlsx]
2022-08-23 Added extra assembly steps
    Added extra detail to assembly steps
2022-09-02 raw pin sensor code
2022-09-02 circuitpuython raw data
2022-10-04 new board cp integration
2022-10-05 motor drivers
2024-01-25 PCB control board
    [AIAB hat BOM.csv, AIAB hat.kicad_pcb, AIAB hat.kicad_sch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]
2024-02-03 Create DexBug.py
    For new development board
2024-02-06 corrected pins
    [AIAB hat.kicad_pcb]
2026-05-06 wheel bot for mujoco
